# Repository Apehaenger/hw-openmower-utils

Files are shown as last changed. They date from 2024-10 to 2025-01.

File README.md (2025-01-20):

# OpenMower Hardware Utils

## V2 Mainboard Compatible

### SATA- Breakout Board for V2 Hardware

<a href="./hw-openmower-utils-satabob/">
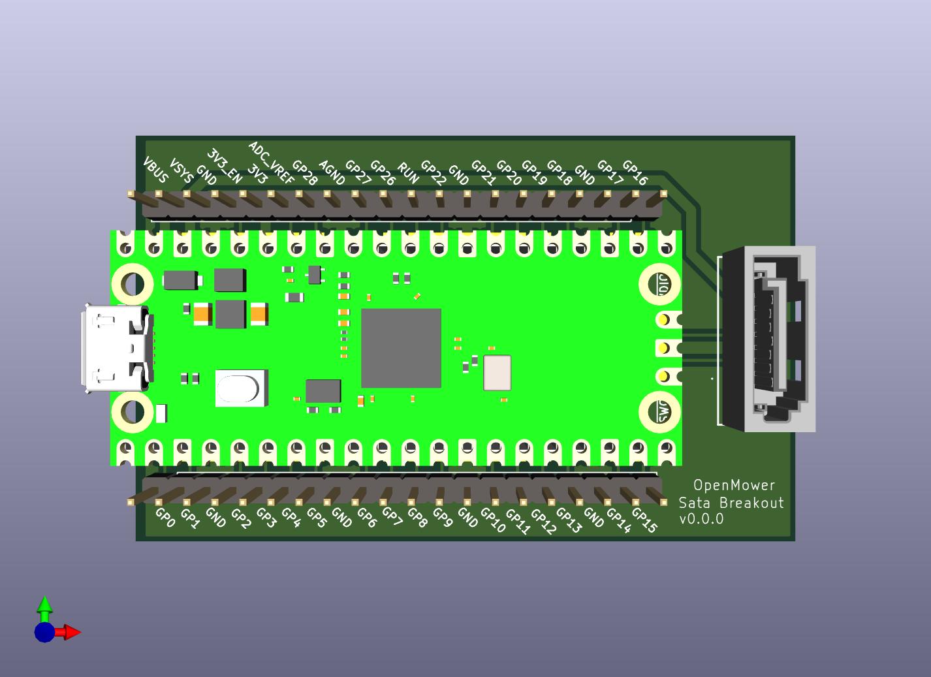
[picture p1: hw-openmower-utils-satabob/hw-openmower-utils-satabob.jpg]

Pico Breakout Board connected via OpenMower's specific SATA plug</a>
<br clear="left"/>

## V1 Mainboard Compatible

### LSM6DSx IMU for V1 Hardware

<a href="./hw-openmower-utils-v1-j20-lsm6dsx/">
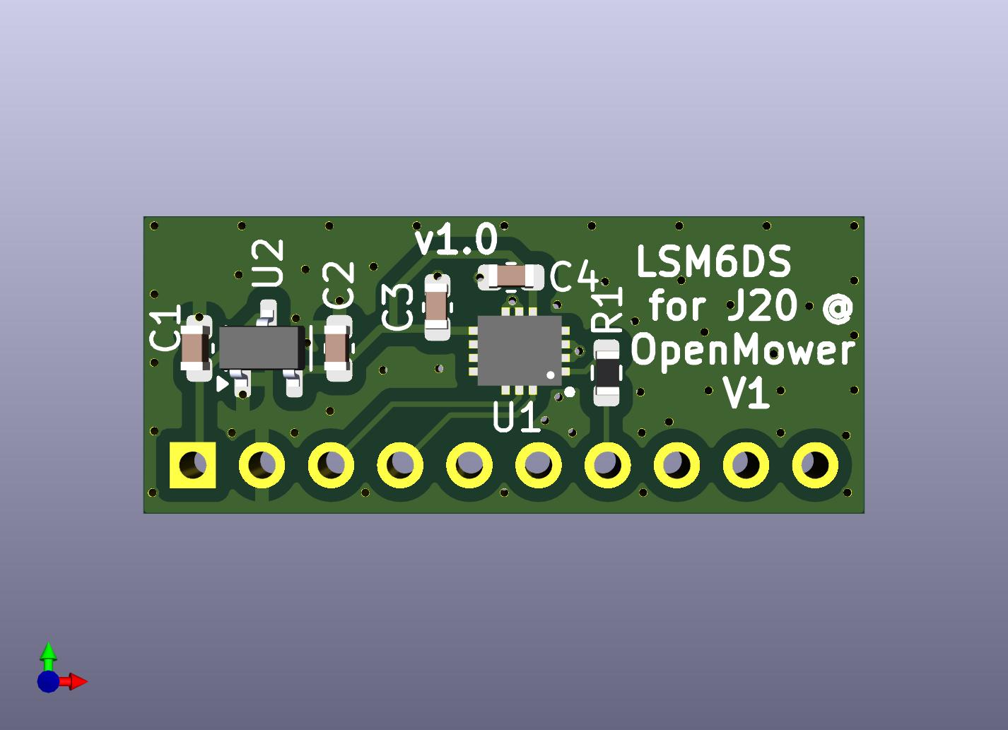
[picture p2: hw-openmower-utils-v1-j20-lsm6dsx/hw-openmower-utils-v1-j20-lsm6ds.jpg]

LSM6DSx IMU alternative for J20 @ OpenMower V1 (instead of MPU9250 or WT901)</a>
<br clear="left"/>

### Arduino/UM9x Shield for V1 Hardware

<a href="./hw-openmower-utils-v1-arduino-uno-um9x/">
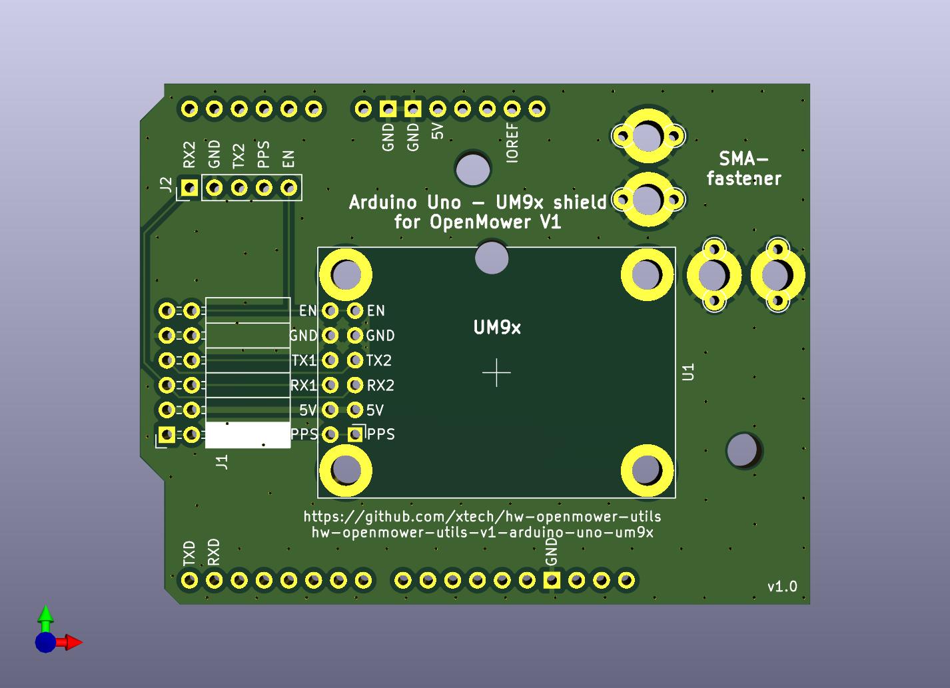
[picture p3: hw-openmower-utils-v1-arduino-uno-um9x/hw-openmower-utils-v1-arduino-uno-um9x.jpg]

Simple UM9x GNSS module mount shield for OpenMower V1</a>
<br clear="left"/>

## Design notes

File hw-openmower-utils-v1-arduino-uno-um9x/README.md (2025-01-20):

# Arduino Uno - UM9x shield for OpenMower V1 Mainboard

Arduino Uno - UM9x shield for OpenMower V1 Mainboard

## Installation

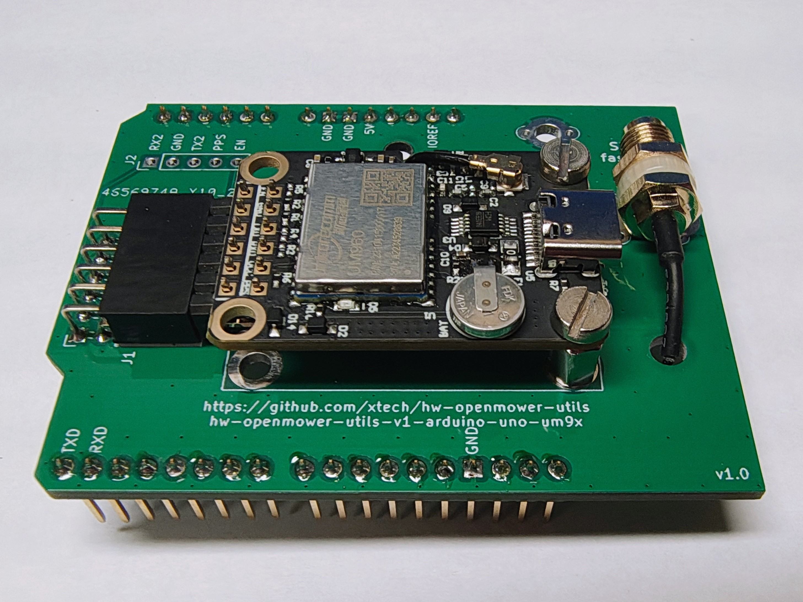
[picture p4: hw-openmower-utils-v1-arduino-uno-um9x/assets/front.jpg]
Front

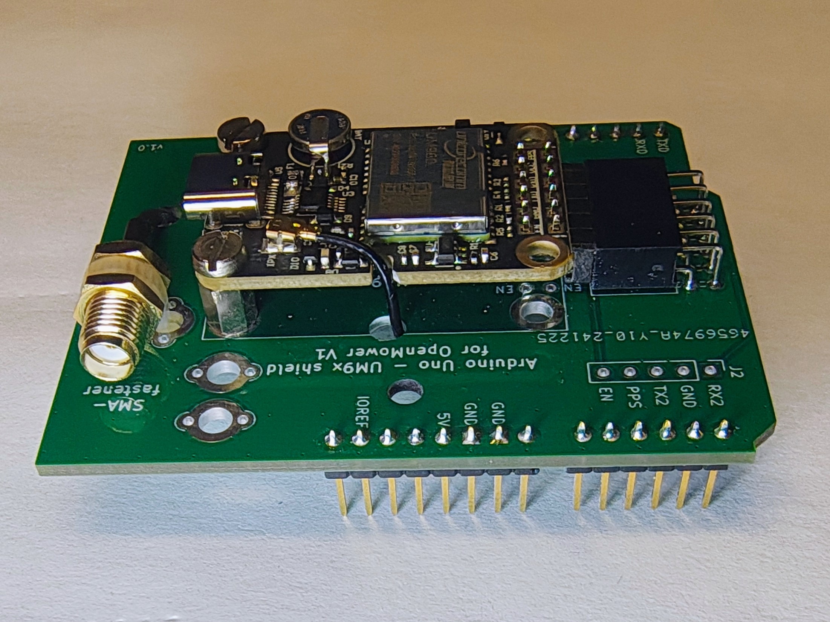
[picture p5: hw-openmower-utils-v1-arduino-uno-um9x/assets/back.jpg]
Back


### Hardware

In the images above, I used 90° pin headers, but you may also use straight ones, in which case the height will be approx. 5mm higher.

As SMA-fastener I used a simple cable straps, but you can also solder a simple looped- wire and fasten it then there.

### Software

If plugged into OpenMower V1 Mainboard, the UM9x will be available at Raspberry Pi's /dev/ttyAMA1 (like the normal GPS module) and use COM2 of UM9x.

I do configure my UM9x with the following 2 steps:

1. Connect to new UM9x with default baud rate and change to higher baud rate via:<br>
   `miniterm /dev/ttyAMA1 115200 -e` and enter:<br>
   FRESET<kbd>⏎ Enter</kbd><br>
   CONFIG COM2 460800<kbd>⏎ Enter</kbd><br>
   Now exit miniterm via <kbd>Ctrl</kbd> + <kbd>]</kbd><br>

1. Connect again to UM9x but with new/higher baud rate via:<br>
   `miniterm /dev/ttyAMA1 460800 -e` and configure GNSS i.e. via:<br>
   MODE ROVER UAV<kbd>⏎ Enter</kbd><br>
   GPGSV COM2 2<kbd>⏎ Enter</kbd><br>
   GPRMC COM2 1<kbd>⏎ Enter</kbd><br>
   GPGSA COM2 1<kbd>⏎ Enter</kbd><br>
   GPVTG COM2 1<kbd>⏎ Enter</kbd><br>
   GPGGA COM2 0.5<kbd>⏎ Enter</kbd><br>
   SAVECONFIG<kbd>⏎ Enter</kbd><br>
   Exit miniterm via <kbd>Ctrl</kbd> + <kbd>]</kbd><br>

Lastly, you need to adapt your mower_config. Change or add the following two lines:<br>

```
export OM_GPS_PROTOCOL=NMEA
export OM_GPS_BAUDRATE=460800
```

## Availability / Production

Pretty cheap to produce (except shipping). Nothing special.

If interested (and resident in EU), I've probably some spares left (for some €). Contact me @Apehaenger in [Discord](https://discord.gg/jE7QNaSxW7)

<p align="right">(<a href="#readme-top">back to top</a>)</p>

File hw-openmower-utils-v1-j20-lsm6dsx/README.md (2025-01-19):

# LSM6DSx IMU for J20 @ V1 Mainboard

LSM6DS for J20 @ OpenMower V1

## Motivation

OpenMower V1 Mainboard 0.9.x up to 0.10.x requires an external plugged in IMU into J20.<br>
Unfortunately you don't get a non-faked MPU9250 anymore, so the only alternative you had, is the (non-cheap) WT901 for which you also need to solder an adapter (if you don't wanna block your sound option).

That's why I designed this alternative.

## Compatibility

I used and tested this only on an OpenMower (V1) 0.9.x Mainboard, but it should be compatible also for 0.9.x up to 0.13.x Mainboard variants.
So you should be also able to use it for the case that you've a damaged or malfunction mainboard-assembled IMU (if you disable/remove the assembled one before).

## Installation

Plug into J20 (take attention to Pin-1 direction) and install Firmware with "_LSM6DSO" suffix (for 0.9.x up to 0.11.x). As of 0.12.x LSM6DSO is compiled in by default.

## Availability / Production

Due to the LGA package of LSM6DSx, PCBA production is relatively expensive in special for lower number of pieces (<20).

Please contact me at `joerg` at `ebeling` dot `ws`, I've probably some tested prototypes with an assembled LSM6DSO left for sell.<br>
If you're good in Hot-Plate soldering, I also have some prototypes without assembled LSM6DSO...

<p align="right">(<a href="#readme-top">back to top</a>)</p>

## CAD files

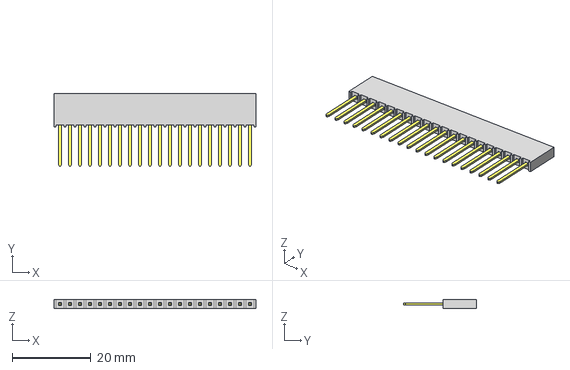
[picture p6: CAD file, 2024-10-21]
hw-openmower-utils-satabob/components/3dmodels/Connectors/SSW-120-23-G-S.stp
51.3 x 18.5 x 2.41 mm
T1SSW-120-23-G-S
P2SSW-120-23-G-S

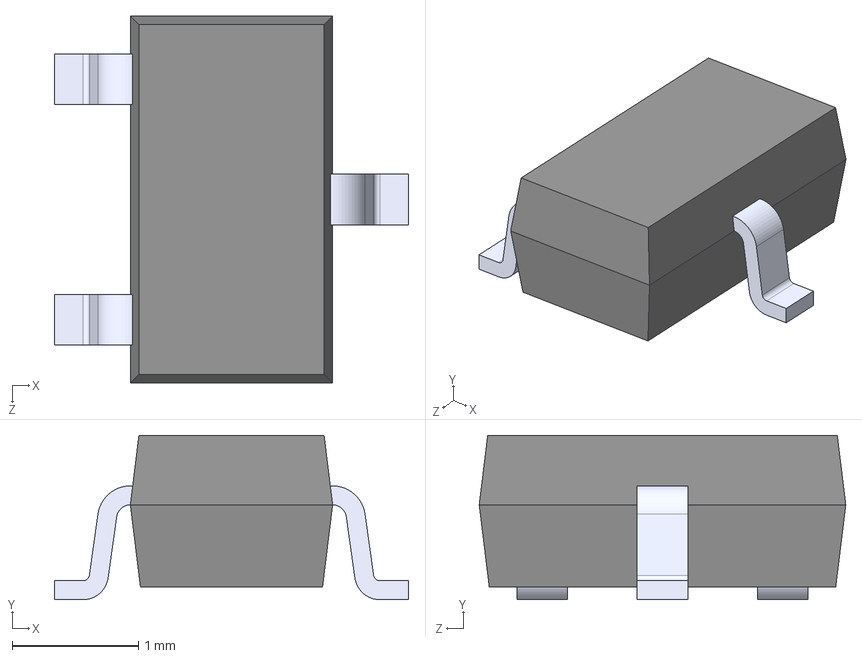
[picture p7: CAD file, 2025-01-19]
hw-openmower-utils-v1-j20-lsm6dsx/3dmodels/XC6206P332MR-G.STEP
2.80 x 1.30 x 2.90 mm

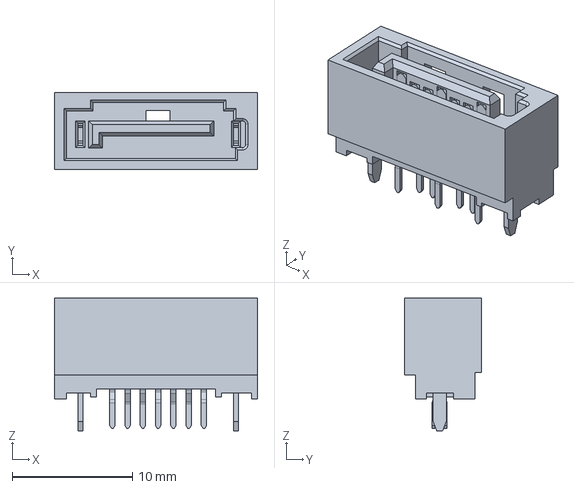
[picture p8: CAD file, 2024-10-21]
hw-openmower-utils-satabob/components/3dmodels/Connectors/SATA.stp
16.9 x 6.45 x 11.1 mm

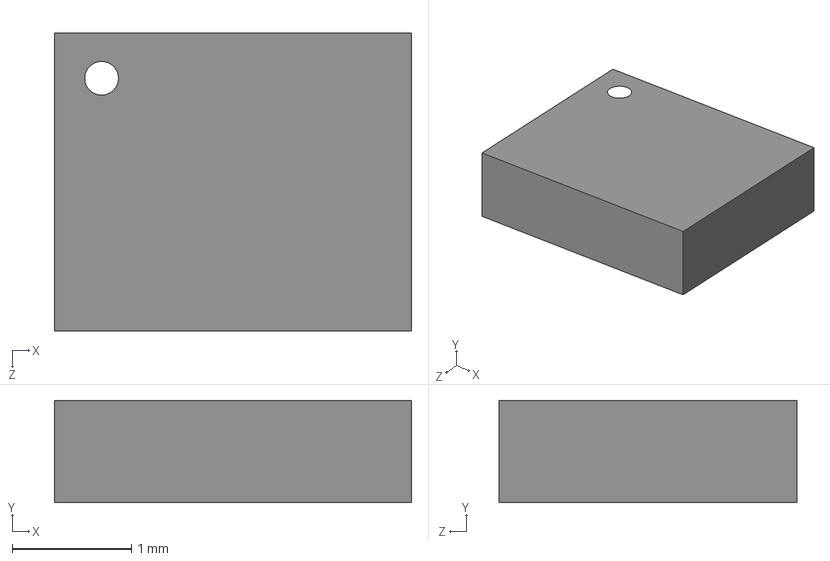
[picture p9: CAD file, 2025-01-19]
hw-openmower-utils-v1-j20-lsm6dsx/3dmodels/LSM6DSOTR.step
3.00 x 0.86 x 2.50 mm

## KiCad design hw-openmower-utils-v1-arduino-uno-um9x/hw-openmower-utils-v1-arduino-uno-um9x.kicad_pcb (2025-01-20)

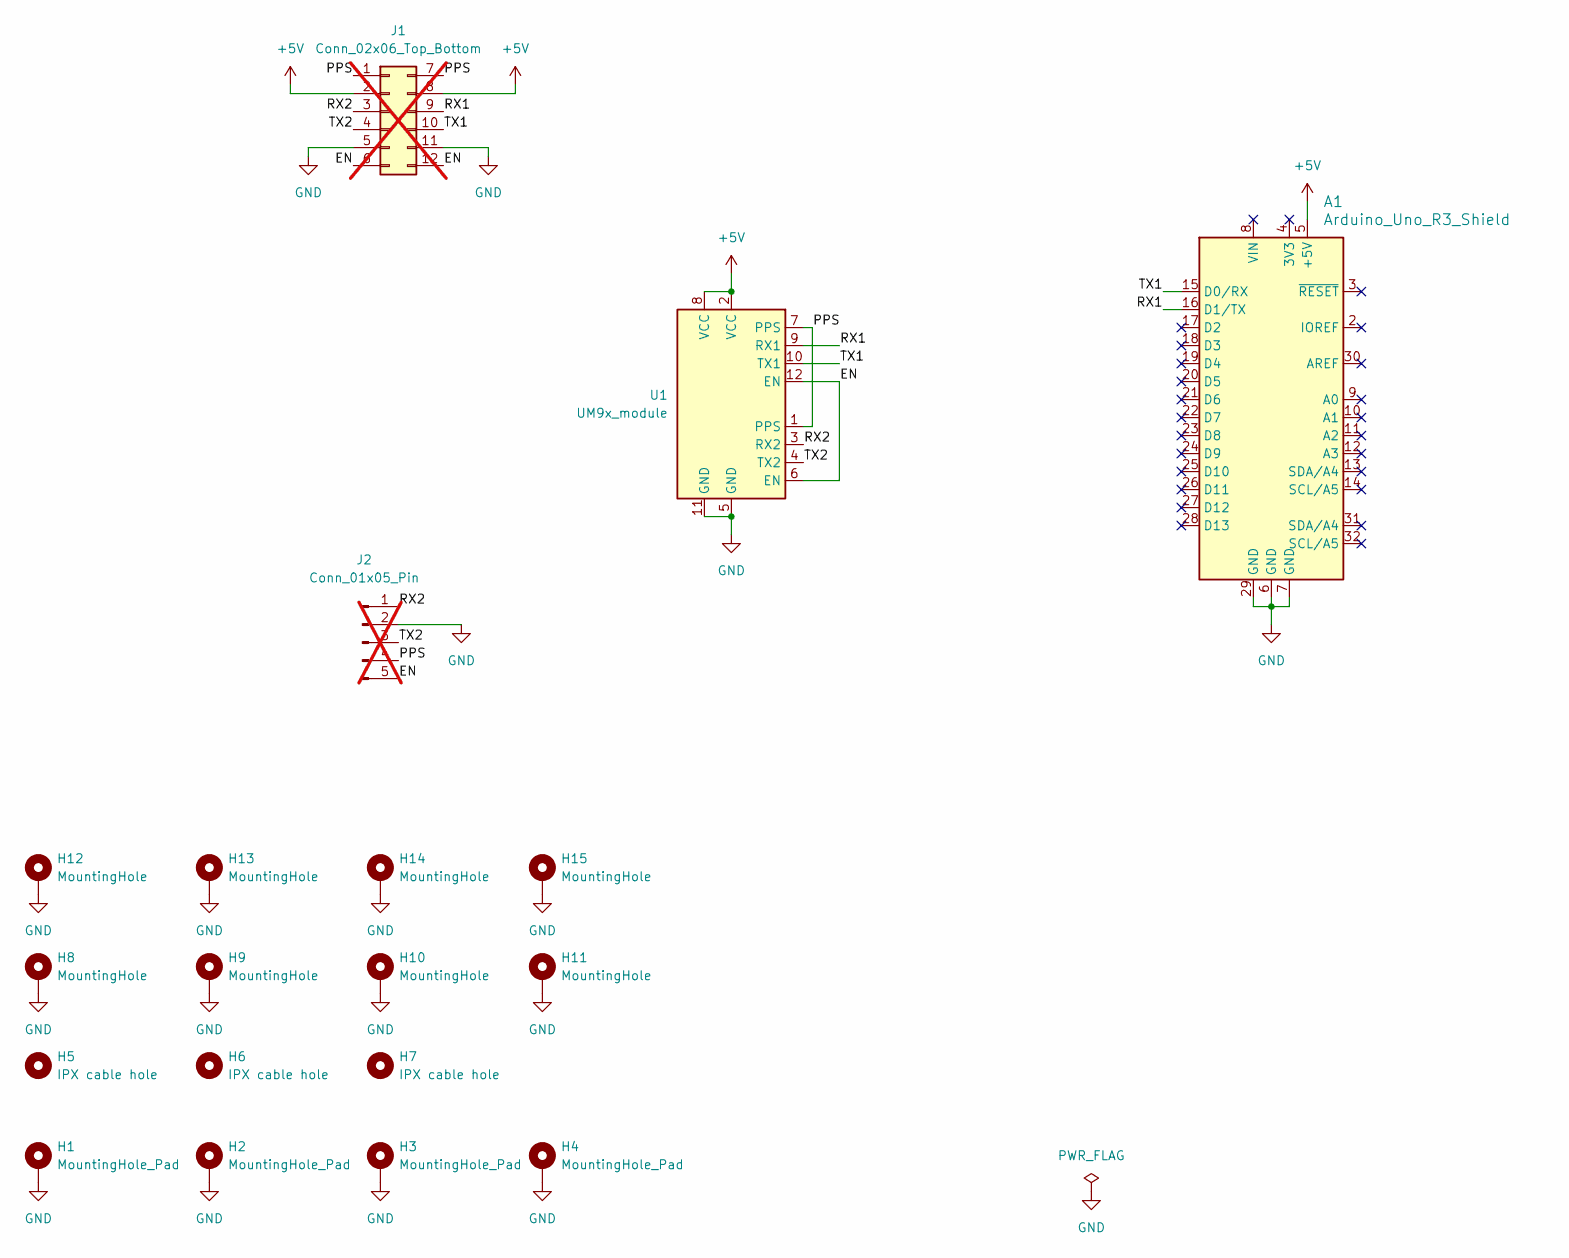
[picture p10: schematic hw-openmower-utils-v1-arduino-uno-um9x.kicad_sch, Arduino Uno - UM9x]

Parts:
A1: Arduino_Uno_R3_Shield; Arduino_Uno_R3_OpenMower_Shield
H1, H2, H3, H4: MountingHole_Pad; MountingHole_3.2mm_M3_DIN965_Pad_TopBottom
H5, H6, H7: IPX cable hole; MountingHole_3.2mm_M3
H8, H9, H10, H11, H12, H13, H14, H15: MountingHole; TestPoint_THTPad_D2.0mm_Drill1.0mm
J1: Conn_02x06_Top_Bottom; PinSocket_2x06_P2.54mm_Horizontal_Top_Bottom; not fitted
J2: Conn_01x05_Pin; PinHeader_1x05_P2.54mm_Vertical; not fitted
U1: UM9x_module

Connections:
+5V: A1.5 (+5V), J1.2, J1.8, U1.2 (VCC), U1.8 (VCC)
/EN: J1.6, J1.12, J2.5, U1.6 (EN), U1.12 (EN)
/PPS: J1.1, J1.7, J2.4, U1.1 (PPS), U1.7 (PPS)
/RX1: A1.16 (D1/TX), J1.9, U1.9 (RX1)
/RX2: J1.3, J2.1, U1.3 (RX2)
/TX1: A1.15 (D0/RX), J1.10, U1.10 (TX1)
/TX2: J1.4, J2.3, U1.4 (TX2)
GND: A1.6 (GND), A1.7 (GND), A1.29 (GND), H1.1, H2.1, H3.1, H4.1, H8.1, H9.1, H10.1, H11.1, H12.1, H13.1, H14.1, H15.1, J1.5, J1.11, J2.2, U1.5 (GND), U1.11 (GND)

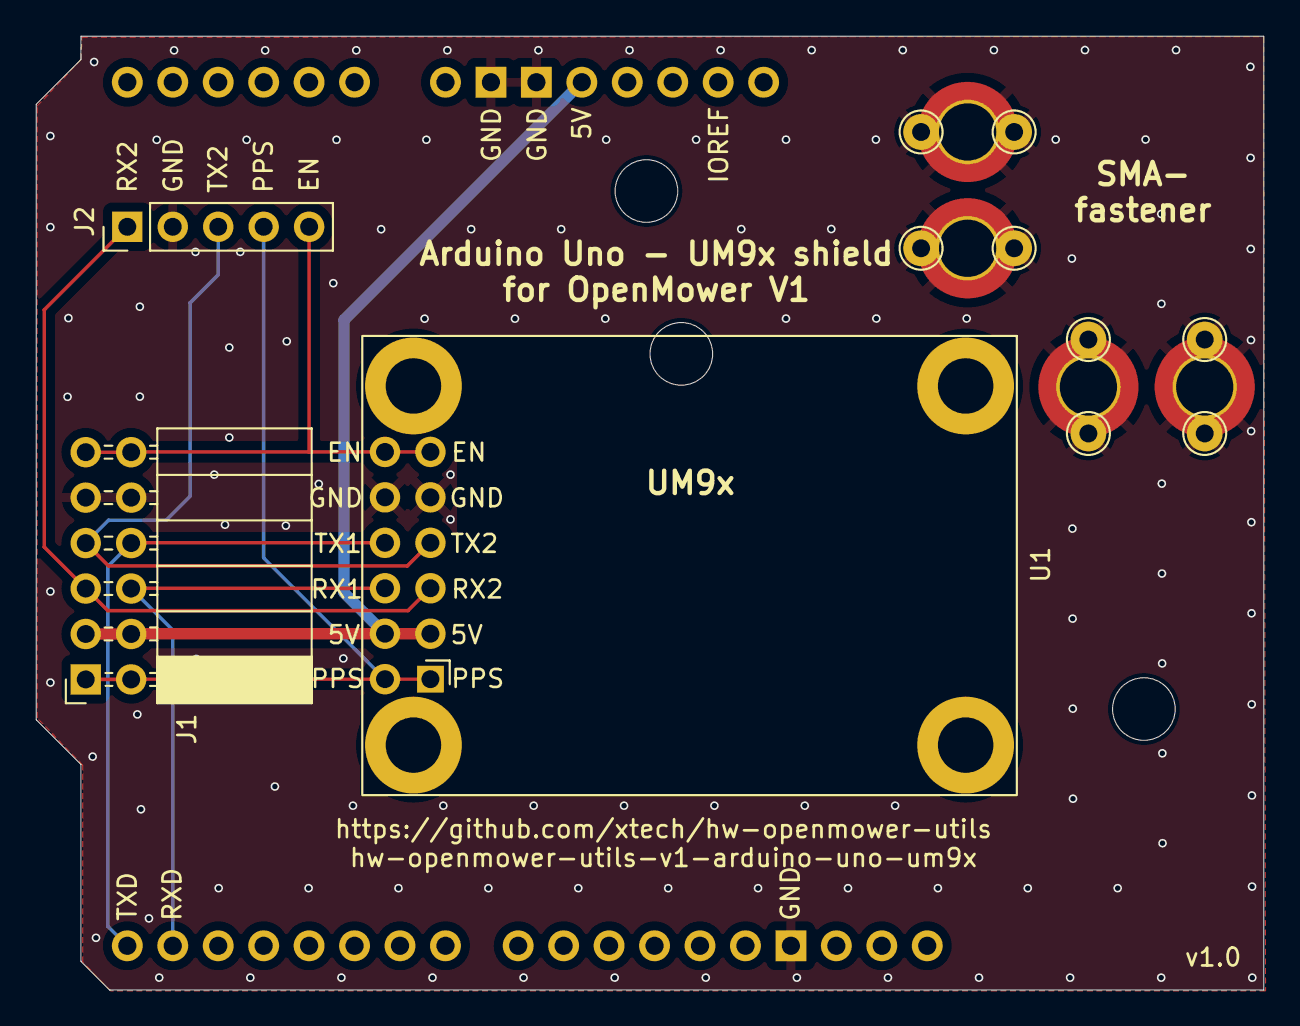
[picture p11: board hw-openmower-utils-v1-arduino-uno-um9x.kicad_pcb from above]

Board: 2 copper layers, 68.6 x 53.3 mm, 19 parts (0 on the bottom side), 8 nets.

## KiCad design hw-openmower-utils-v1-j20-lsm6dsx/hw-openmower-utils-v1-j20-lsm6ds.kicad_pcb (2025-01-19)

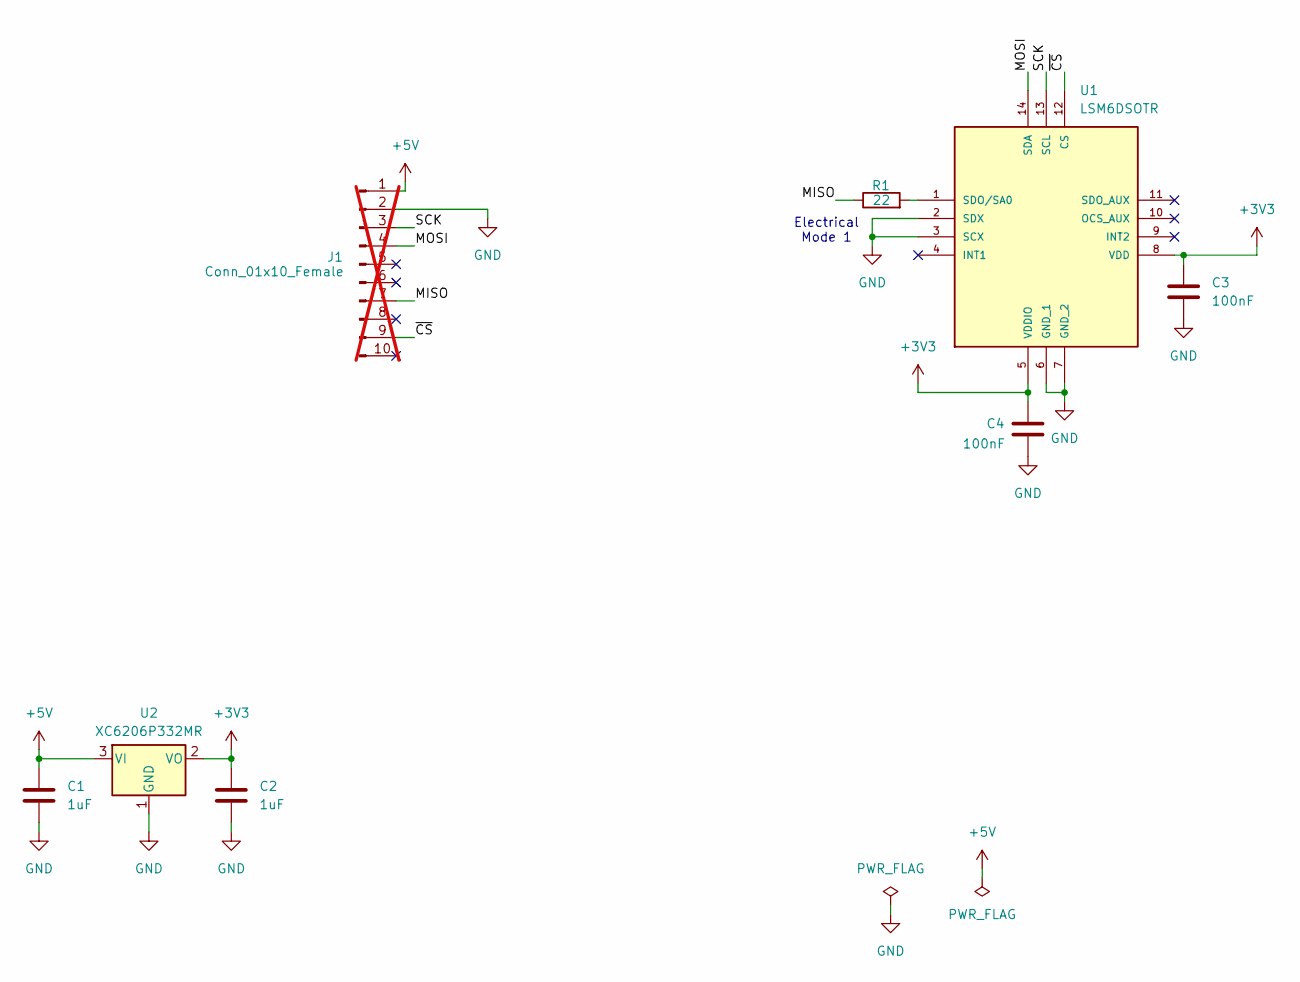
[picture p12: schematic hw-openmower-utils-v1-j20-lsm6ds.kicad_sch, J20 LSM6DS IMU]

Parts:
C1, C2: 1uF; C_0603_1608Metric; LCSC C15849
C3, C4: 100nF; C_0603_1608Metric; LCSC C14663
J1: Conn_01x10_Female; PinHeader_1x10_P2.54mm_Vertical; Part Number PZ254-1-10-Z-8.5; LCSC C2894933; not fitted
R1: 22; R_0603_1608Metric; LCSC C23345
U1: LSM6DSOTR; LCSC C2655100
U2: XC6206P332MR; SOT-23-3; LCSC C347376

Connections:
+3V3: C2.1, C3.1, C4.1, U1.5 (VDDIO), U1.8 (VDD), U2.2 (VO)
+5V: C1.1, J1.1, U2.3 (VI)
/MISO: J1.7, R1.1
/MOSI: J1.4, U1.14 (SDA)
/SCK: J1.3, U1.13 (SCL)
/~CS: J1.9, U1.12 (CS)
GND: C1.2, C2.2, C3.2, C4.2, J1.2, U1.2 (SDX), U1.3 (SCX), U1.6 (GND_1), U1.7 (GND_2), U2.1 (GND)
unnamed: R1.2, U1.1 (SDO/SA0)

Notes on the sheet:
Electrical Mode 1

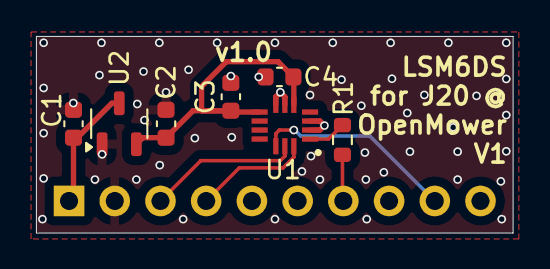
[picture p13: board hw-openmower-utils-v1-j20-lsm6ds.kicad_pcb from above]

Board: 2 copper layers, 26.5 x 10.9 mm, 8 parts (1 on the bottom side), 8 nets.

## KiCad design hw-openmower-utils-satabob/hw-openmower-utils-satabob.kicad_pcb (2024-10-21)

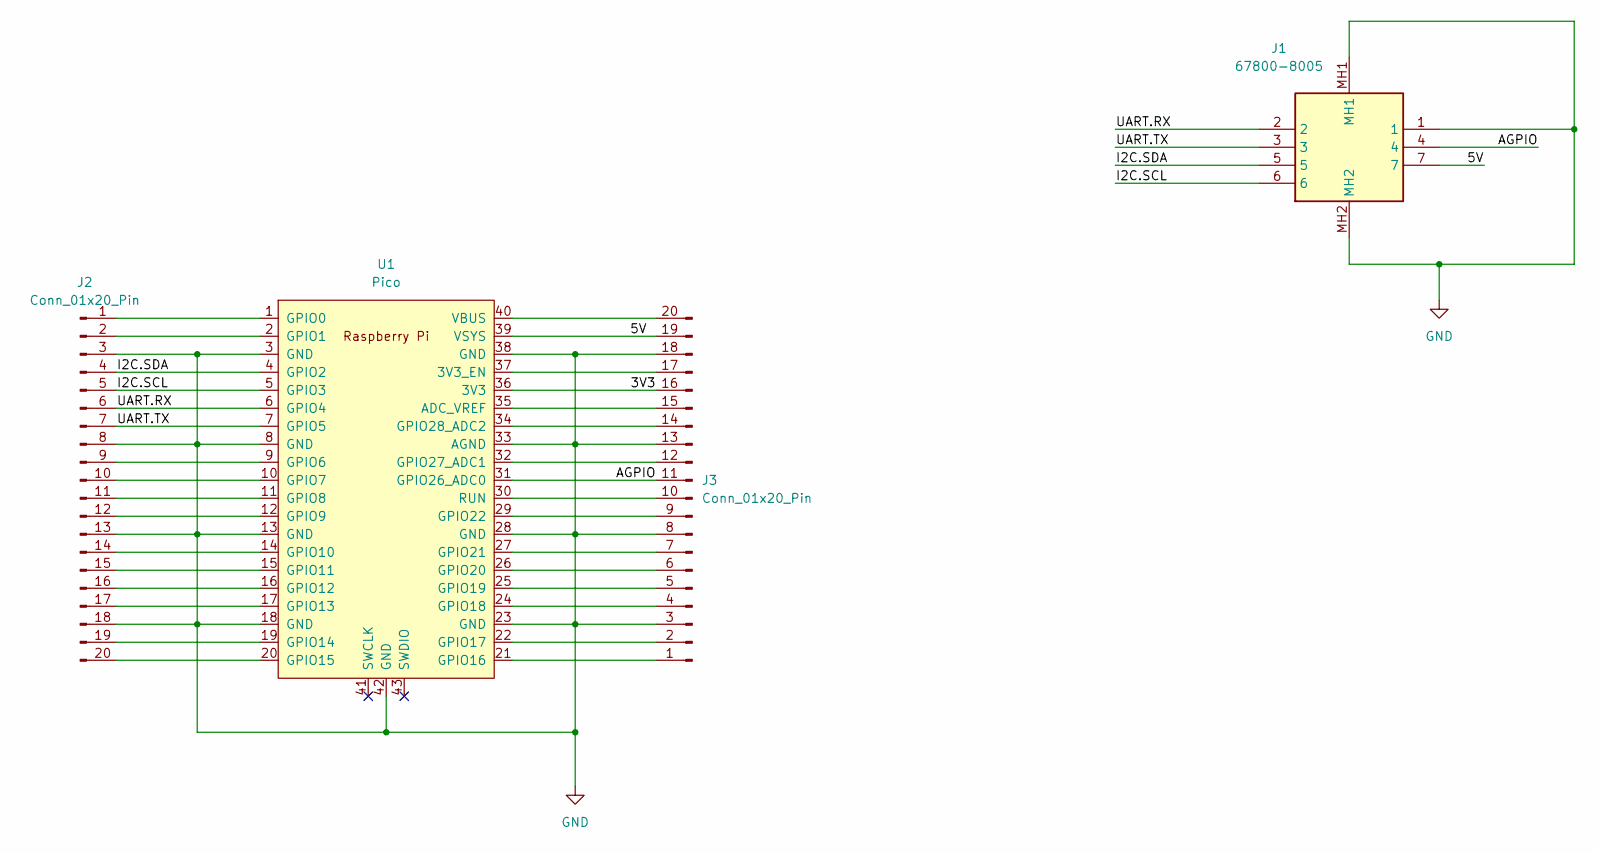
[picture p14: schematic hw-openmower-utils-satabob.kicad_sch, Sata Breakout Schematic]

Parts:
J1: 67800-8005; SATA-Molex-67800-8005; Mouser Part Number 538-67800-8005
J2, J3: Conn_01x20_Pin; PinHeader_1x20_P2.54mm_Vertical
U1: Pico; RPi_Pico_SMD_TH

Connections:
/3V3: J3.16, U1.36 (3V3)
/5V: J1.7, J3.19, U1.39 (VSYS)
/AGPIO: J1.4, J3.11, U1.31 (GPIO26_ADC0)
/I2C.SCL: J1.6, J2.5, U1.5 (GPIO3)
/I2C.SDA: J1.5, J2.4, U1.4 (GPIO2)
/UART.RX: J1.2, J2.6, U1.6 (GPIO4)
/UART.TX: J1.3, J2.7, U1.7 (GPIO5)
GND: J1.1, J1.MH1, J1.MH2, J2.3, J2.8, J2.13, J2.18, J3.3, J3.8, J3.13, J3.18, U1.3 (GND), U1.8 (GND), U1.13 (GND), U1.18 (GND), U1.23 (GND), U1.28 (GND), U1.33 (AGND), U1.38 (GND), U1.42 (GND)
unnamed: J2.1, U1.1 (GPIO0)
unnamed: J2.2, U1.2 (GPIO1)
unnamed: J2.9, U1.9 (GPIO6)
unnamed: J2.10, U1.10 (GPIO7)
unnamed: J2.11, U1.11 (GPIO8)
unnamed: J2.12, U1.12 (GPIO9)
unnamed: J2.14, U1.14 (GPIO10)
unnamed: J2.15, U1.15 (GPIO11)
unnamed: J2.16, U1.16 (GPIO12)
unnamed: J2.17, U1.17 (GPIO13)
unnamed: J2.19, U1.19 (GPIO14)
unnamed: J2.20, U1.20 (GPIO15)
unnamed: J3.1, U1.21 (GPIO16)
unnamed: J3.2, U1.22 (GPIO17)
unnamed: J3.4, U1.24 (GPIO18)
unnamed: J3.5, U1.25 (GPIO19)
unnamed: J3.6, U1.26 (GPIO20)
unnamed: J3.7, U1.27 (GPIO21)
unnamed: J3.9, U1.29 (GPIO22)
unnamed: J3.10, U1.30 (RUN)
unnamed: J3.12, U1.32 (GPIO27_ADC1)
unnamed: J3.14, U1.34 (GPIO28_ADC2)
unnamed: J3.15, U1.35 (ADC_VREF)
unnamed: J3.17, U1.37 (3V3_EN)
unnamed: J3.20, U1.40 (VBUS)

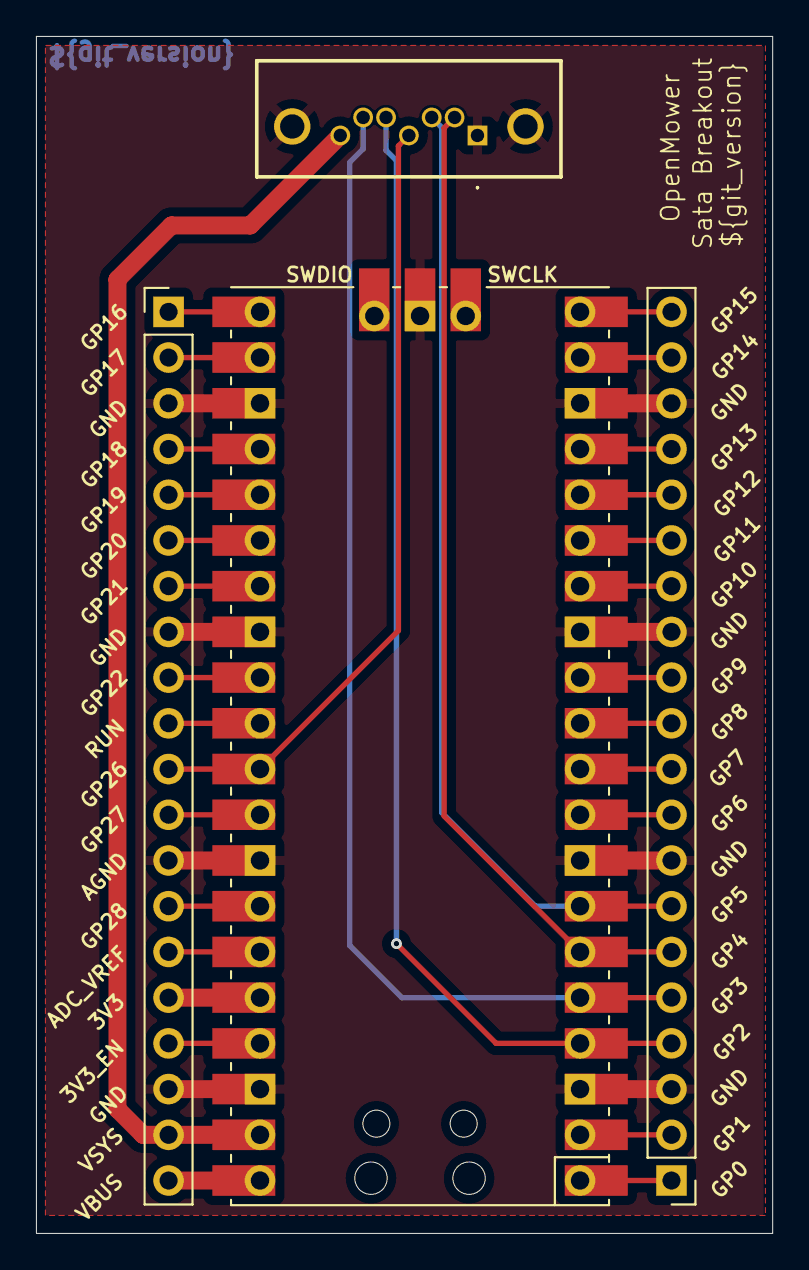
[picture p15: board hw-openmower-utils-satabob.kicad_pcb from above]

Board: 2 copper layers, 40.9 x 66.5 mm, 4 parts (0 on the bottom side), 33 nets.

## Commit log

2024-10-21 Initial commit of sata breakout files
    [hw-openmower-utils-satabob.kicad_pcb, hw-openmower-utils-satabob.kicad_sch]
2024-10-21 Uploading components files
    [SATA.stp, SSW-120-23-G-S.stp]
2024-10-21 added git version to pcb
    [hw-openmower-utils-satabob.kicad_pcb]
2025-01-09 LSM6DSx & docs
    [LSM6DSOTR.step, XC6206P332MR-G.STEP, hw-openmower-utils-v1-j20-lsm6ds.kicad_pcb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]

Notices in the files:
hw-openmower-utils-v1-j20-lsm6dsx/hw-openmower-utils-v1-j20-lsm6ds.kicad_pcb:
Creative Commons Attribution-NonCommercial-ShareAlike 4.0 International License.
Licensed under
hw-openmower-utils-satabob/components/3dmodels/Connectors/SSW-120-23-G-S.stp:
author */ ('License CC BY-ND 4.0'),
